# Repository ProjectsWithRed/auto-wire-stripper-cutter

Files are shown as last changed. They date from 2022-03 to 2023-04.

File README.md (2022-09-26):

# Automatic Wire Stripper and Cutter

A 3D printed automatic wire stripper and cutter. You simply choose your measurements on a screen, press a button, and it does it all for you. It will strip the wire and cut the wire depending on the options you chose.

There is a [video](https://youtu.be/pbuzLy1ktKM) associated with this repository/project, I highly recommend watching it before using this repo.

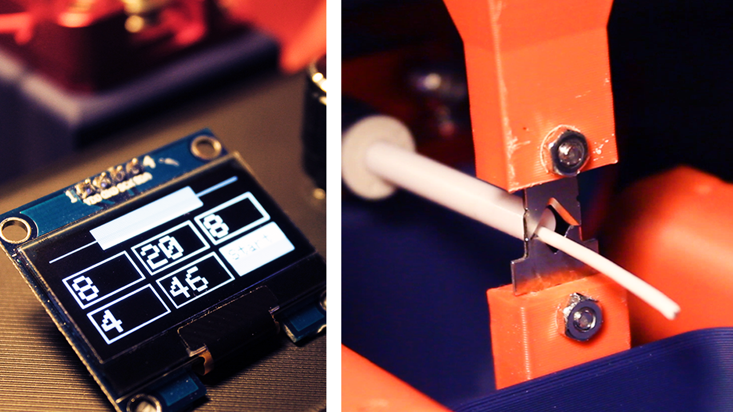
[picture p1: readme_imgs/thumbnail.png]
Video (https://youtu.be/pbuzLy1ktKM "Automatic_wire_stripper_cutter")


# Arduino

You can find the Arduino sketch in the `/AutoWireCutterStripper` directory.

- Make sure that the i2c address (`#define i2c_Address 0x3c`), corresponds to your OLED display i2c address, which you will find in the datasheet of your OLED display.

## Libraries needed

All these libraries can be easily installed using the Arduino IDE library manager.

- `Stepper` by Arduino.
- `Encoder` by Paul Stoffregen.
- `Adafruit GFX Library` by Adafruit.
- `Adafruit SH110X` by Adafruit.

# Components

- [ESP32](https://www.amazon.co.uk/dp/B071P98VTG?ref_=cm_sw_r_cp_ud_dp_DDGQ5R6XVBCC7JBB04K3), for the micro-controller. When uploading code, ensure that you hold down the on board BOOT button on the ESP32.
- [12V 5A](https://www.amazon.co.uk/dp/B08GS7WM1Z?ref_=cm_sw_r_cp_ud_dp_QJHEPBDAWDEDX3JDRTGF) power supply.
- [LM2596](https://www.amazon.co.uk/dp/B077VW4BTY?ref_=cm_sw_r_cp_ud_dp_1D9J5V36PP85VKDA2V49) or any step down converter, to convert 12V to 5V for the ESP32.
- [Nema 17 stepper motor](https://www.amazon.co.uk/dp/B07K3Y5314?ref_=cm_sw_r_cp_ud_dp_RZY0XHJFQ6YN1HZXPX8X) (x3), two for the linear motion, one for the extruder.
- [A4988 stepper motor driver](https://www.amazon.co.uk/dp/B06Y23YXD5?ref_=cm_sw_r_cp_ud_dp_1REVFHTFN5E2CMNSRTTB) (x3), to drive and control the stepper motors.
- 100uF capacitor (x3), for the 12V power pins for each of the A4988 drivers.
- [OLED display](https://www.amazon.co.uk/dp/B078J78R45?ref_=cm_sw_r_cp_ud_dp_1XXX2M7YAQJN5G6AKV93), 1.3inch, 128x64.
- [Rotary encoder](https://www.amazon.co.uk/dp/B07CMSHWV6?ref_=cm_sw_r_cp_ud_dp_Y2VC355RTHHYRKTZ436B) with button.
- [Power switch](https://www.amazon.co.uk/dp/B01N2U8PK0?ref_=cm_sw_r_cp_ud_dp_K4GSW1GDA4G8QCXJWPE4), to turn on and off.
- [3D printer filament extruder](https://www.amazon.co.uk/dp/B07TWK8FRN?ref_=cm_sw_r_cp_ud_dp_FXQD93NZKYG9VA0Q6P3F), for the wire feeder.
- [D8mm L100mm lead screw](https://www.amazon.co.uk/dp/B07QWKG317?ref_=cm_sw_r_cp_ud_dp_JMAC4EKE28W5Z3GSZSN8) (x2), for the linear motion.
- [D8mm lead screw nut](https://www.amazon.co.uk/dp/B07QWKG317?ref_=cm_sw_r_cp_ud_dp_JMAC4EKE28W5Z3GSZSN8) (x2), to attach the top blade housing to the lead screws.
- [5x8mm rigid shaft coupler](https://www.amazon.co.uk/dp/B096G1GZH5?ref_=cm_sw_r_cp_ud_dp_VWE1T2SQZQB0X13TQ1F7) (x2), to attach the lead screws to the stepper motors.
- [10mm magnets](https://www.amazon.co.uk/dp/B08FSTRRDR?ref_=cm_sw_r_cp_ud_dp_13WEC590XVADQKN2RJ0W) (x2), to attach the container.
- [KNIPEX V-blades](https://www.amazon.co.uk/dp/B00161GBDW?ref_=cm_sw_r_cp_ud_dp_S63KK1ZZ8DPRHWMBEFJC), to cut and strip the wires.

# Wiring

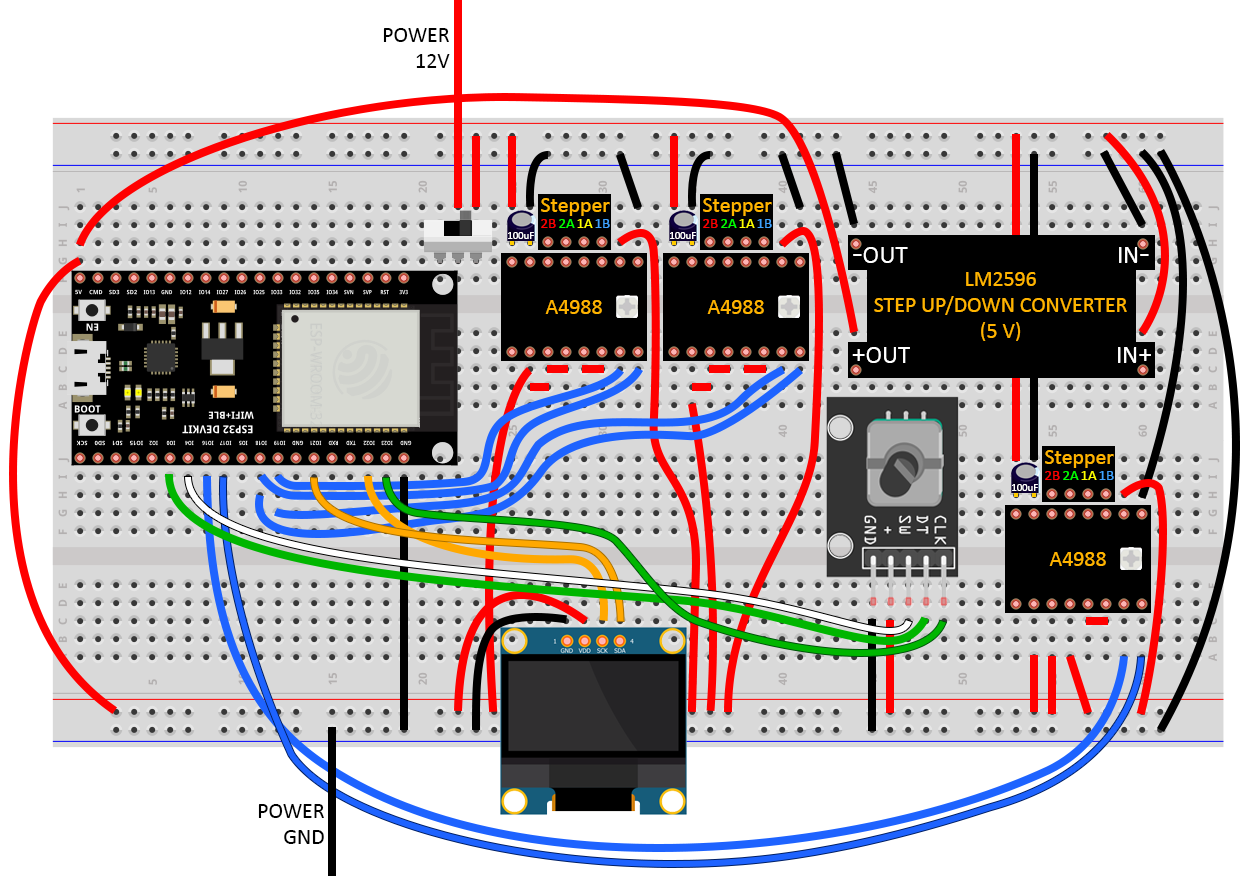
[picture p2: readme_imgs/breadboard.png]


# 3D printing

Please refer to the `/3d_printing` directory.

# Assembly layout
This is the layout of the components on the board. Use this only for reference on roughly where you should fix the components to the board. I don't suggest using this for exact measurements as you should position the components where it is appropriate for your version of the project.

[Layout PDF](./assembly_layout.pdf).

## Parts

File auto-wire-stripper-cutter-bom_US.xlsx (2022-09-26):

QTY | PN | Description | Cost/EA | Cost/EXT | Link | Notes
1 | ‎B08HMJ1X6W | ESP32-WROOM-32D | $19.59 | $19.59 | https://www.amazon.com/AITRIP-ESP32-DevKitC-Development-ESP32-WROOM-32D-Compatible/dp/B08HMJ1X6W | Micro Controller (Just get the three pack. You'll use em.)
1 | HTY-1205000 | DC 12V 5A Switching Power Supply | $13.88 | $13.88 | https://www.amazon.com/SUPERNIGHT-100V-Switching-Supply-Adapter/dp/B008FKDK2M | 12V 5A Power Supply
1 | B07L915WKX | LM2596 Adjustable Voltage Regulator | $9.09 | $9.09 | https://www.amazon.com/Aokin-Adjustable-Regulator-Converter-Voltmeter/dp/B07L915WKX | 12V to 5V Step Down for ESP32
1 | B088BLQYDX | Nema 17 Stepper Motor,42x23mm 42BYGH, 3 pack | $25.99 | $25.99 | https://www.amazon.com/Stepper-42x23mm-42BYGH-130mN-m-Printer/dp/B088BLQYDX | 2x Linear, 1x Extruder
1 | A4988 | HiLetgo 5pcs A4988 | $9.89 | $9.89 | https://www.amazon.com/HiLetgo-Stepstick-Stepper-Printer-Compatible/dp/B07BND65C8 | Stepper Motor Driver
1 | A-0002-F01f | Cap, Electrolytic, 100uF, 25V, 6 pack | $6.24 | $6.24 | https://www.amazon.com/Projects-Radial-Electrolytic-Capacitor-100uF/dp/B07YN6NX4H | For the 12V power pins for each of the A4988 drivers.
1 | 14284330 | OLED Display SSD1106 128x64 Pixels i2c | $12.49 | $12.49 | https://www.amazon.com/MakerFocus-128X64-1-3-Inch-SSD1106/dp/B08V97FYD2 | Display For machine
1 | KY-040 | Rotary Encoder Module KY-040, w Knob | $13.99 | $13.99 | https://www.amazon.com/TELESKY-Encoder-Potentiometers-%EF%BC%8815%C3%9716-5-Arduino/dp/B09T3CQ758 | Encoder to control
1 | U16F5 | Latching Illuminated 12V 5A Power Switch | $8.99 | $8.99 | https://www.amazon.com/Ulincos-Latching-Button-Suitable-Mounting/dp/B07FVHRM1F | Power Switch
1 | RDX3D030B-PASFQ | Redrex Ender 3 Extruder | $10.99 | $10.99 | https://www.amazon.com/dp/B08CS9THQL?th=1 | Wire Extruder
1 | a19032000ux0497 | 2X 100mm Lead Screw w/ Nut | $11.99 | $11.99 | https://www.amazon.com/uxcell-Stainless-Copper-Thread-Printer/dp/B07QX4KP8Y | Linear Motion for Guillotine (Lead Screw and Nut Combo)
1 | 0791783537158 | 2X 5mm to 8mm rigid coupler | $8.54 | $8.54 | https://www.amazon.com/Zeberoxyz-Coupling-Aluminum-Diameter-Connector/dp/B08ZJ854Z6 | Linear NEMA 17 Coupler
1 | B09XMHCLYG | 30X 10x2mm magnets | $7.99 | $7.99 | https://www.amazon.com/Fridge-Magnets-Refrigerator-Neodymium-Whiteboard/dp/B09XMHCLYG | For attaching container
1 | 12 69 21 | Blades for Knipex 12 62 180 | $17.87 | $17.87 | https://www.amazon.com/KNIPEX-12-69-21-Blades/dp/B005GYL20M | For Cutting Wires…and things…
 |  |  |  | $177.53
1 | B094HYN8T2 | 4x4 Matrix Keypad, 6 pack | $8.99 | $8.99 | https://www.amazon.com/Keypad-Membrane-Keyboard-Arduino-Microcontroller/dp/B094HYN8T2 | For direct data input
https://github.com/ProjectsWithRed/auto-wire-stripper-cutter

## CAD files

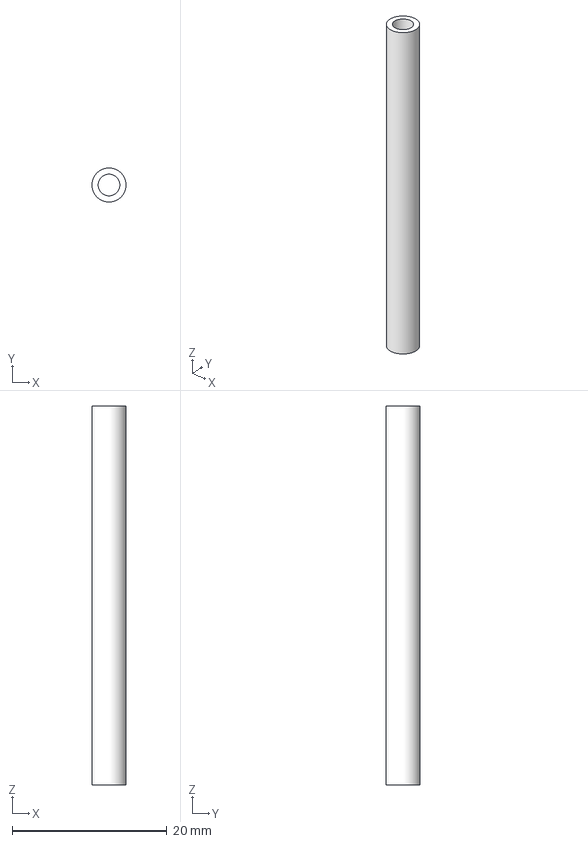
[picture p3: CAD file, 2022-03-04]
3d_printing/wire_channel.3mf
4.40 x 4.40 x 49.0 mm

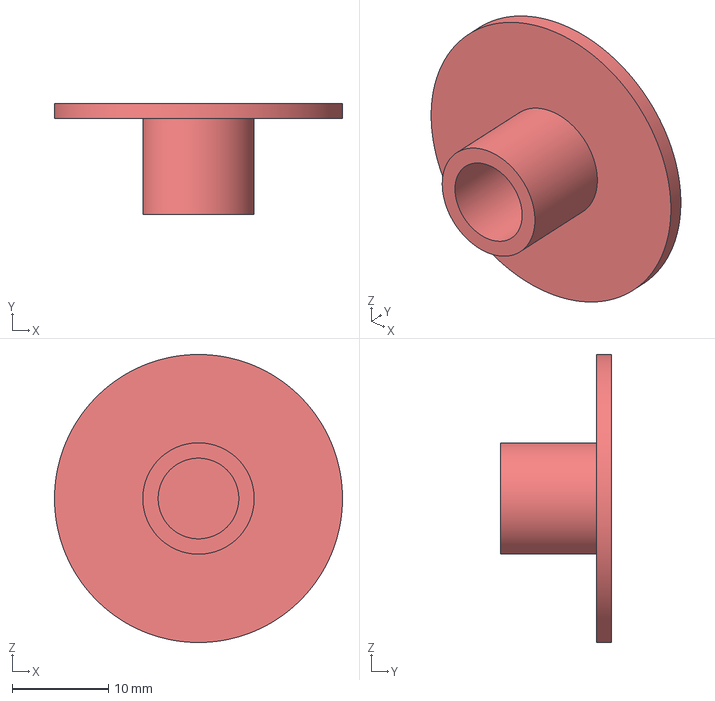
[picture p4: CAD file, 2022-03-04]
3d_printing/spoolHolder_cylinder_cap.3mf
30.0 x 11.6 x 30.0 mm

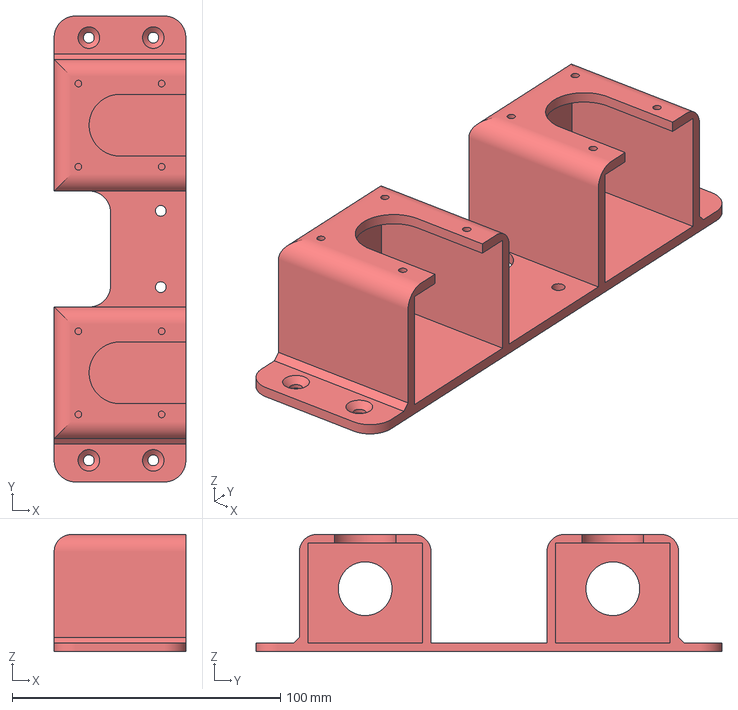
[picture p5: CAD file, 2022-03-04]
3d_printing/linearMotion_motorsHousing.3mf
49.0 x 173.6 x 43.6 mm

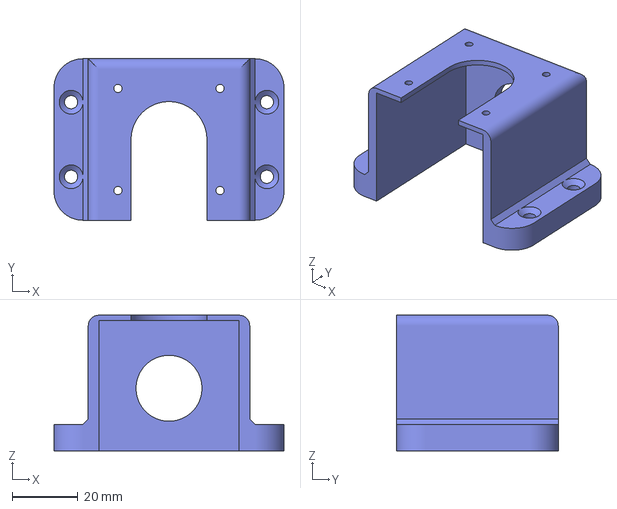
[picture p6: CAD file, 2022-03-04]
3d_printing/extruderStepper_housing.3mf
69.8 x 49.0 x 41.2 mm

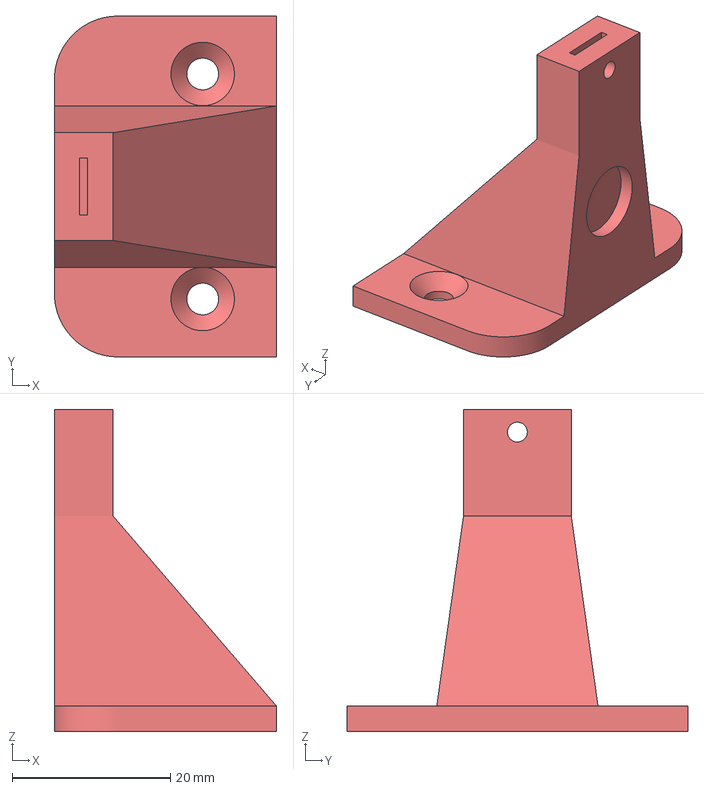
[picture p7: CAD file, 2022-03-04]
3d_printing/bottomBlade_housing.3mf
28.0 x 43.0 x 40.6 mm

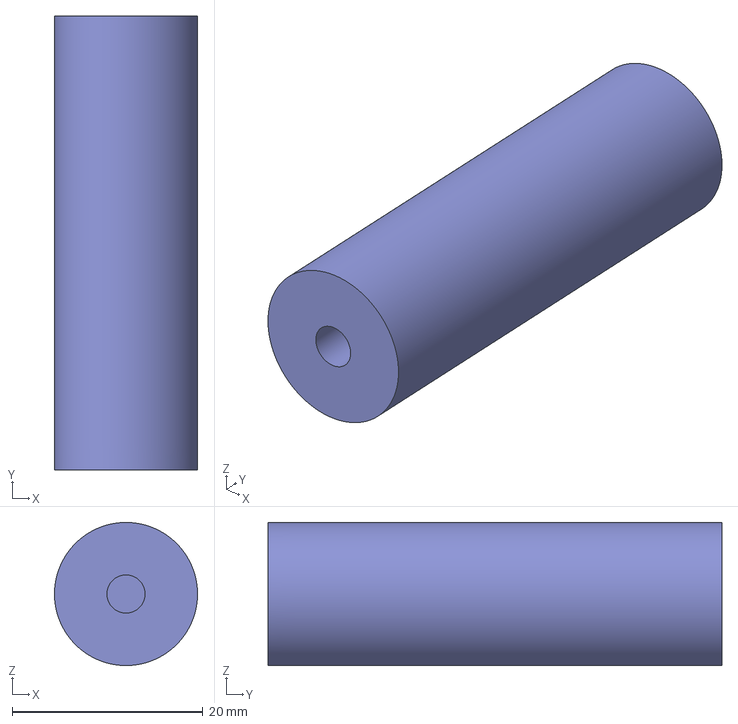
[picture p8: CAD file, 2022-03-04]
3d_printing/spoolHolder_cylinder.3mf
15.0 x 47.6 x 15.0 mm

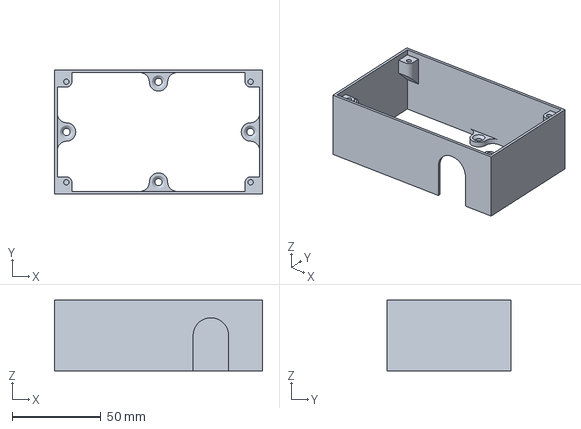
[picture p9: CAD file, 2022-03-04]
3d_printing/wiring_housing.3mf
117.4 x 70.2 x 40.0 mm

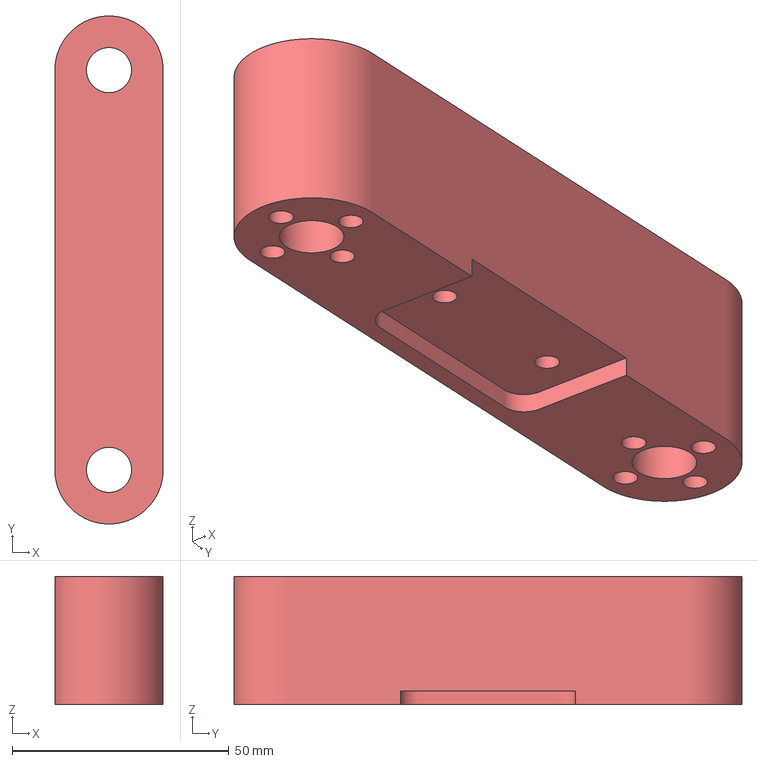
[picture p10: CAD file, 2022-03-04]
3d_printing/linearMotion_attachment.3mf
25.0 x 117.2 x 29.6 mm

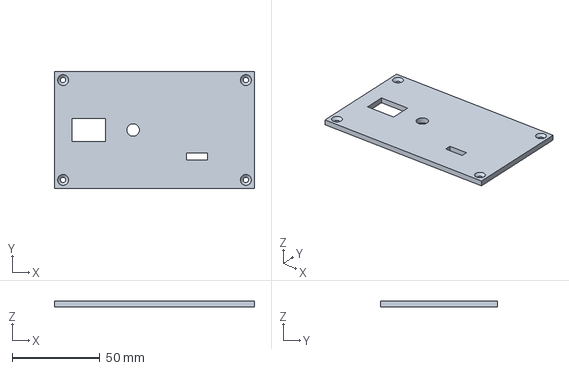
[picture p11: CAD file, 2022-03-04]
3d_printing/wiring_housing_lid.3mf
113.8 x 66.6 x 3.20 mm

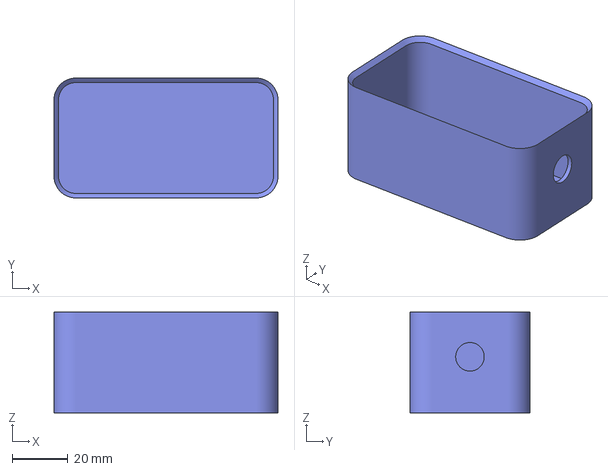
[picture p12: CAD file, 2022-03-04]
3d_printing/container.3mf
80.0 x 42.8 x 36.0 mm

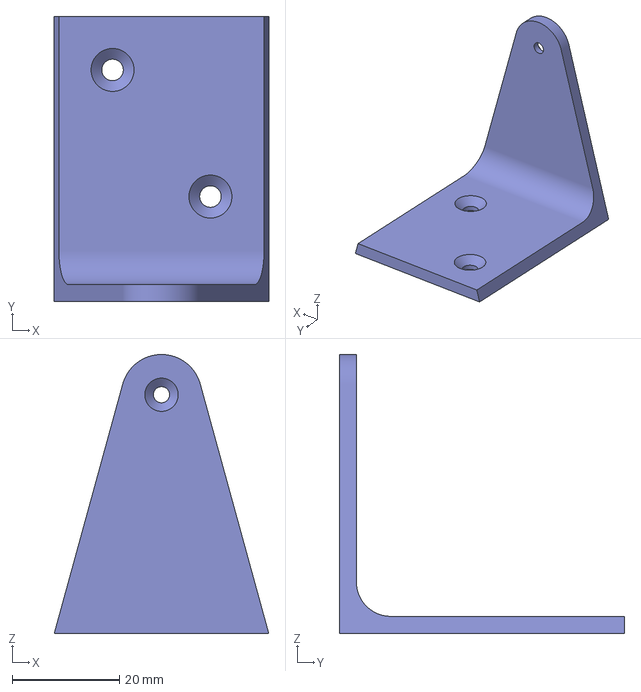
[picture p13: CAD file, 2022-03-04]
3d_printing/spoolHolder_base.3mf
40.0 x 53.2 x 52.0 mm

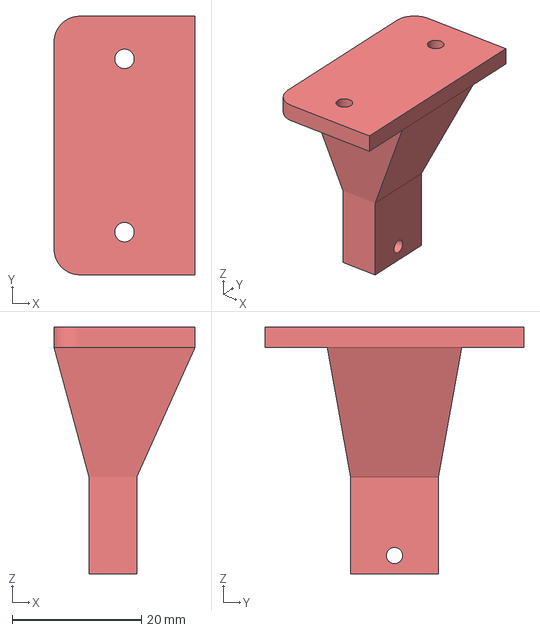
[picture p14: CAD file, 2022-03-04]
3d_printing/topBlade_housing.3mf
21.8 x 40.0 x 38.2 mm

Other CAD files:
3d_printing/stl/bottomBlade_housing.stl
3d_printing/stl/container.stl
3d_printing/stl/extruderStepper_housing.stl
3d_printing/stl/spoolHolder_base.stl
3d_printing/stl/spoolHolder_cylinder.stl
3d_printing/stl/spoolHolder_cylinder_cap.stl
3d_printing/stl/topBlade_housing.stl
3d_printing/stl/wiring_housing.stl
3d_printing/stl/wiring_housing_lid.stl

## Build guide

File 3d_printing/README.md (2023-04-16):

# 3D printing

All the 3D printed parts used in this project.

- `/stl`, same models but in stl format.
- `assembly_model.step`, the full design in `.step` format.

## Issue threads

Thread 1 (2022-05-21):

PCB layout and assembly installation layout

umalave, 2022-05-21:
Hi, do you have a PCB layout for this project? also, do you have the layout where you attached the threaded insert on the wood board?

ProjectsWithRed, 2022-05-23:
Hi,

I did not create a PCB layout for this project.

Regarding the assembly layout, I just added a PDF (ee4eb457c4b8973d444eb9b3b2031fe7ea3d9ca9) showing the assembly layout. However, I recommend using it only for reference on roughly where you should fix the components to the board. I don't suggest using this for exact measurements as you should position the components where it is appropriate for your version of the project.

Closed 2022-07-25.

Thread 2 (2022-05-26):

Printable baseplate with heat set inserts

fryertruck, 2022-05-26:
I really appreciate your work in this project and thinking about building one.

What do you think about adding a printable base to your project? Of course the positions would then be fixed, but I don't see an Issue with that.

I can help you out with creating the file, but need correct measurements for that.

ProjectsWithRed, 2022-06-22:
I have uploaded a file `assembly_layout.pdf` that shows all the measurements on the board, feel free do make a printable base 👍🏼.

Closed 2022-07-25.

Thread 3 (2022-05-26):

Let the machine remove part of the Insulation

fryertruck, 2022-05-26:
Is it possible that the machine also directly removes the insulation from the front part of the cable? Before the blade goes up again, the extruder would have to pull back for this in the first step.

Can you perhaps test this?

ProjectsWithRed, 2022-06-22:
You can easily achieve this with minimal changes to the code and if done correctly should work with no issues. Feel free to experiement, as I unfortunately don't have time to do it.

ProjectsWithRed, 2022-07-25:
Inactive.

Closed 2022-07-25.

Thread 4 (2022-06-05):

Having issues loading the code. Can you help, please?

umalave, 2022-06-05:
Arduino: 1.8.19 (Windows 10), Board: "DOIT ESP32 DEVKIT V1, 80MHz, 115200, None"

AutoWireCutterStripper:60:71: error: stray '\302' in program

   <title>auto-wire-stripper-cutter/AutoWireCutterStripper.ino at main · ProjectsWithRed/auto-wire-stripper-cutter · GitHub</title>

                                                                       ^

AutoWireCutterStripper:60:72: error: stray '\267' in program

   <title>auto-wire-stripper-cutter/AutoWireCutterStripper.ino at main · ProjectsWithRed/auto-wire-stripper-cutter · GitHub</title>

                                                                        ^

AutoWireCutterStripper:60:116: error: stray '\302' in program

   <title>auto-wire-stripper-cutter/AutoWireCutterStripper.ino at main · ProjectsWithRed/auto-wire-stripper-cutter · GitHub</title>

                                                                                                                    ^

AutoWireCutterStripper:60:117: error: stray '\267' in program

   <title>auto-wire-stripper-cutter/AutoWireCutterStripper.ino at main · ProjectsWithRed/auto-wire-stripper-cutter · GitHub</title>

                                                                                                                     ^

C:\Users\myuser\Desktop\AutoWireCutterStripper\AutoWireCutterStripper.ino:411:10: warning: missing terminating ' character

     <!-- '"` --><!-- </textarea></xmp> --></option></form><form class="js-site-search-form" role="search" aria-label="Site" data-scope-type="Repository" data-scope-id="466200308" data-scoped-search-url="/ProjectsWithRed/auto-wire-stripper-cutter/search" data-owner-scoped-search-url="/users/ProjectsWithRed/search" data-unscoped-search-url="/search" data-turbo="false" action="/ProjectsWithRed/auto-wire-stripper-cutter/search" accept-charset="UTF-8" method="get">

          ^

AutoWireCutterStripper:411:10: error: missing terminating ' character

     <!-- '"` --><!-- </textarea></xmp> --></option></form><form class="js-site-search-form" role="search" aria-label="Site" data-scope-type="Repository" data-scope-id="466200308" data-scoped-search-url="/ProjectsWithRed/auto-wire-stripper-cutter/search" data-owner-scoped-search-url="/users/ProjectsWithRed/search" data-unscoped-search-url="/search" data-turbo="false" action="/ProjectsWithRed/auto-wire-stripper-cutter/search" accept-charset="UTF-8" method="get">

          ^~~~~~~~~~~~~~~~~~~~~~~~~~~~~~~~~~~~~~~~~~~~~~~~~~~~~~~~~~~~~~~~~~~~~~~~~~~~~~~~~~~~~~~~~~~~~~~~~~~~~~~~~~~~~~~~~~~~~~~~~~~~~~~~~~~~~~~~~~~~~~~~~~~~~~~~~~~~~~~~~~~~~~~~~~~~~~~~~~~~~~~~~~~~~~~~~~~~~~~~~~~~~~~~~~~~~~~~~~~~~~~~~~~~~~~~~~~~~~~~~~~~~~~~~~~~~~~~~~~~~~~~~~~~~~~~~~~~~~~~~~~~~~~~~~~~~~~~~~~~~~~~~~~~~~~~~~~~~~~~~~~~~~~~~~~~~~~~~~~~~~~~~~~~~~~~~~~~~~~~~~~~~~~~~~~~~~~~~~~~~~~~~~~~~~~~~~~~~~~~~~~~~~~~~~~~~~~~~~~~~~~~~~~~~~~~~~~~~~~~~~~~~~~~~~~~~~~

AutoWireCutterStripper:468:75: error: stray '\342' in program

       <span aria-hidden="true" class="d-inline-block ml-1 v-align-middle">↵</span>

                                                                           ^

AutoWireCutterStripper:468:76: error: stray '\206' in program

       <span aria-hidden="true" class="d-inline-block ml-1 v-align-middle">↵</span>

                                                                            ^

AutoWireCutterStripper:468:77: error: stray '\265' in program

       <span aria-hidden="true" class="d-inline-block ml-1 v-align-middle">↵</span>

                                                                             ^

AutoWireCutterStripper:473:56: error: stray '\342' in program

       <span class="d-inline-block ml-1 v-align-middle">↵</span>

                                                        ^

AutoWireCutterStripper:473:57: error: stray '\206' in program

       <span class="d-inline-block ml-1 v-align-middle">↵</span>

                                                         ^

AutoWireCutterStripper:473:58: error: stray '\265' in program

       <span class="d-inline-block ml-1 v-align-middle">↵</span>

                                                          ^

AutoWireCutterStripper:515:75: error: stray '\342' in program

       <span aria-hidden="true" class="d-inline-block ml-1 v-align-middle">↵</span>

                                                                           ^

AutoWireCutterStripper:515:76: error: stray '\206' in program

       <span aria-hidden="true" class="d-inline-block ml-1 v-align-middle">↵</span>

                                                                            ^

AutoWireCutterStripper:515:77: error: stray '\265' in program

       <span aria-hidden="true" class="d-inline-block ml-1 v-align-middle">↵</span>

                                                                             ^

AutoWireCutterStripper:520:56: error: stray '\342' in program

       <span class="d-inline-block ml-1 v-align-middle">↵</span>

                                                        ^

AutoWireCutterStripper:520:57: error: stray '\206' in program

       <span class="d-inline-block ml-1 v-align-middle">↵</span>

                                                         ^

AutoWireCutterStripper:520:58: error: stray '\265' in program

       <span class="d-inline-block ml-1 v-align-middle">↵</span>

                                                          ^

AutoWireCutterStripper:553:75: error: stray '\342' in program

       <span aria-hidden="true" class="d-inline-block ml-1 v-align-middle">↵</span>

                                                                           ^

AutoWireCutterStripper:553:76: error: stray '\206' in program

       <span aria-hidden="true" class="d-inline-block ml-1 v-align-middle">↵</span>

                                                                            ^

AutoWireCutterStripper:553:77: error: stray '\265' in program

       <span aria-hidden="true" class="d-inline-block ml-1 v-align-middle">↵</span>

                                                                             ^

AutoWireCutterStripper:558:56: error: stray '\342' in program

       <span class="d-inline-block ml-1 v-align-middle">↵</span>

                                                        ^

AutoWireCutterStripper:558:57: error: stray '\206' in program

       <span class="d-inline-block ml-1 v-align-middle">↵</span>

                                                         ^

AutoWireCutterStripper:558:58: error: stray '\265' in program

       <span class="d-inline-block ml-1 v-align-middle">↵</span>

                                                          ^

AutoWireCutterStripper:591:75: error: stray '\342' in program

       <span aria-hidden="true" class="d-inline-block ml-1 v-align-middle">↵</span>

                                                                           ^

AutoWireCutterStripper:591:76: error: stray '\206' in program

       <span aria-hidden="true" class="d-inline-block ml-1 v-align-middle">↵</span>

                                                                            ^

AutoWireCutterStripper:591:77: error: stray '\265' in program

       <span aria-hidden="true" class="d-inline-block ml-1 v-align-middle">↵</span>

                                                                             ^

AutoWireCutterStripper:596:56: error: stray '\342' in program

       <span class="d-inline-block ml-1 v-align-middle">↵</span>

                                                        ^

AutoWireCutterStripper:596:57: error: stray '\206' in program

       <span class="d-inline-block ml-1 v-align-middle">↵</span>

                                                         ^

AutoWireCutterStripper:596:58: error: stray '\265' in program

       <span class="d-inline-block ml-1 v-align-middle">↵</span>

                                                          ^

C:\Users\umala\Desktop\AutoWireCutterStripper\AutoWireCutterStripper.ino:977:25: warning: missing terminating " character

             data-action="

                         ^

AutoWireCutterStripper:977:25: error: missing terminating " character

AutoWireCutterStripper:978:41: error: stray '#' in program

               input-entered:ref-selector#inputEntered

                                         ^

AutoWireCutterStripper:979:40: error: stray '#' in program

               tab-selected:ref-selector#tabSelected

                                        ^

AutoWireCutterStripper:980:38: error: stray '#' in program

               focus-list:ref-selector#focusFirstListMember

                                      ^

C:\Users\umala\Desktop\AutoWireCutterStripper\AutoWireCutterStripper.ino:981:13: warning: missing terminating " character

             "

             ^

AutoWireCutterStripper:981:13: error: missing terminating " character

C:\Users\umala\Desktop\AutoWireCutterStripper\AutoWireCutterStripper.ino:1028:25: warning: missing terminating " character

             data-action="

                         ^

AutoWireCutterStripper:1028:25: error: missing terminating " character

AutoWireCutterStripper:1029:41: error: stray '#' in program

               input-entered:ref-selector#inputEntered

                                         ^

AutoWireCutterStripper:1030:40: error: stray '#' in program

               tab-selected:ref-selector#tabSelected

                                        ^

AutoWireCutterStripper:1031:38: error: stray '#' in program

               focus-list:ref-selector#focusFirstListMember

                                      ^

C:\Users\umala\Desktop\AutoWireCutterStripper\AutoWireCutterStripper.ino:1032:13: warning: missing terminating " character

             "

             ^

AutoWireCutterStripper:1032:13: error: missing terminating " character

AutoWireCutterStripper:1398:71: error: stray '#' in program

           <td id="LC1" class="blob-code blob-code-inner js-file-line">#<span class="pl-k">include</span> <span class="pl-s"><span class="pl-pds">&lt;</span>Stepper.h<span class="pl-pds">&gt;</span></span></td>

                                                                       ^

AutoWireCutterStripper:1402:71: error: stray '#' in program

           <td id="LC2" class="blob-code blob-code-inner js-file-line">#<span class="pl-k">include</span> <span class="pl-s"><span class="pl-pds">&lt;</span>Encoder.h<span class="pl-pds">&gt;</span></span></td>

                                                                       ^

AutoWireCutterStripper:1406:71: error: stray '#' in program

           <td id="LC3" class="blob-code blob-code-inner js-file-line">#<span class="pl-k">include</span> <span class="pl-s"><span class="pl-pds">&lt;</span>SPI.h<span class="pl-pds">&gt;</span></span></td>

                                                                       ^

AutoWireCutterStripper:1410:71: error: stray '#' in program

           <td id="LC4" class="blob-code blob-code-inner js-file-line">#<span class="pl-k">include</span> <span class="pl-s"><span class="pl-pds">&lt;</span>Wire.h<span class="pl-pds">&gt;</span></span></td>

                                                                       ^

AutoWireCutterStripper:1414:71: error: stray '#' in program

           <td id="LC5" class="blob-code blob-code-inner js-file-line">#<span class="pl-k">include</span> <span class="pl-s"><span class="pl-pds">&lt;</span>Adafruit_GFX.h<span class="pl-pds">&gt;</span></span></td>

                                                                       ^

AutoWireCutterStripper:1418:71: error: stray '#' in program

           <td id="LC6" class="blob-code blob-code-inner js-file-line">#<span class="pl-k">include</span> <span class="pl-s"><span class="pl-pds">&lt;</span>Adafruit_SH110X.h<span class="pl-pds">&gt;</span></span></td>

                                                                       ^

AutoWireCutterStripper:1427:71: error: stray '#' in program
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

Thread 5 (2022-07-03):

Arduino Programming issue

JoeKingSid, 2022-07-03:
Hello, I cannot seem to connect to my ESP board to upload the Sketch.  I think it is because I do not have the correct board selected.  I purchased this board [https://www.amazon.com/dp/B09J95SMG7?ref=ppx_yo2ov_dt_b_product_details&th=1](url) installed the required libraries but upon upload get an error message that states my board is not connected.  FYI... I have connected power, the screen and the pot on a breadboard just to keep things simple to start.  Can you advise what I need to do to get my Board to talk to my Computer?  Thanks!

JoeKingSid, 2022-07-04:
Here is a screen shot of the error message as well as my Board Config

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
g

JoeKingSid, 2022-07-04:
1 More shot of Device Manager recognizing the port 5 connection.  Thanks in advance for any advice/help!
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

ProjectsWithRed, 2022-07-04:
Try selecting "ESP32 Dev Module" as the board. Also press and hold the boot button on the ESP32 when you press upload.

JoeKingSid, 2022-07-04:
Well, actually I might have spoken a bit too soon ...  I found this thing in Arduino called Serial Monitor...  it seems to show that the Controller has some kind of error and is stuck in some kind of a Reboot Loop...  this is what it says...

ELF file SHA256: 0000000000000000

Rebooting...
ets Jul 29 2019 12:21:46

rst:0xc (SW_CPU_RESET),boot:0x13 (SPI_FAST_FLASH_BOOT)
configsip: 0, SPIWP:0xee
clk_drv:0x00,q_drv:0x00,d_drv:0x00,cs0_drv:0x00,hd_drv:0x00,wp_drv:0x00
mode:DIO, clock div:1
load:0x3fff0030,len:1344
load:0x40078000,len:13516
load:0x40080400,len:3604
entry 0x400805f0
E (121) gpio: esp_ipc_call_blocking failed (0x103)
E (121) gpio: gpio_install_isr_service(449): GPIO isr service already installed
Guru Meditation Error: Core  0 panic'ed (LoadProhibited). Exception was unhandled.

Core  0 register dump:
PC      : 0x400ee48b  PS      : 0x00060533  A0      : 0x800d4d4f  A1      : 0x3ffe3b20
A2      : 0x00000000  A3      : 0x3ffc1c38  A4      : 0x3ffc1c38  A5      : 0x00060523
A6      : 0x00060520  A7      : 0x00000001  A8      : 0x800d490c  A9      : 0x3ffe3ae0
A10     : 0x3ffbdca4  A11     : 0x00800000  A12     : 0x00000017  A13     : 0x3ffe3b20
A14     : 0x007bdc90  A15     : 0x003fffff  SAR     : 0x00000009  EXCCAUSE: 0x0000001c
EXCVADDR: 0x00000000  LBEG    : 0x400865e5  LEND    : 0x400865f5  LCOUNT  : 0xfffffff7

Backtrace:0x400ee488:0x3ffe3b200x400d4d4c:0x3ffe3b40 0x400d2cf4:0x3ffe3b70 0x400d2d75:0x3ffe3ba0 0x400d13b9:0x3ffe3bc0 0x400d15b9:0x3ffe3be0 0x400d96ab:0x3ffe3c10 0x40082ce1:0x3ffe3c40 0x4007920a:0x3ffe3c90  |<-CORRUPTED

ELF file SHA256: 0000000000000000

Rebooting...
ets Jul 29 2019 12:21:46

rst:0xc (SW_CPU_RESET),boot:0x13 (SPI_FAST_FLASH_BOOT)

It just keeps repeating that over and over.  Any ideas???  I wish you would make a video showing details of how to upload the INO cause so far everything else has been straightforward but, to a NOOB like me, the Arduino programming is not very intuitive.  THANKS!!!

ProjectsWithRed, 2022-07-08:
@JoeKingSid Someone had this similar problem, please see issue #4. To fix it, try uploading the code using the Arduino web IDE.

JoeKingSid, 2022-07-23:
UPDATE... First let me say thanks for the suggestions thus far!  To date I have still not been able to get the project working. :-( I was able to upload code via the Online Web Editor and I think that part is complete but honestly I'm not sure. After uploading the code I was expecting to see my OLED display light up with something but, No Joy.  I decided to start from scratch and these are the steps I took...
1. Connect the ESP32 to the Computer via USB cable.
2. Upload Code
3. Place ESP32 chip on Breadboard and connect  12vdc adapter to Stepdown Converter
4. verify 5vdc on stepdown and connect  5vdc wires as shown on diagram to ESP32 & OLED display
5. Connect OLED SDK & SDA  to ESP Pins 21 & 22 as shown
6. Connect Pot/Encoder to 5VDC (as shown) & SW, DT & SDK to ESP32 Pins  as shown.

applied power to circuit - nothing
pressed enable button on ESP32 - nothing
pressed boot button on ESP32 -nothing

Tried Re-uploading the code - nothing

Not really sure what else to try as this seems to be the "bare bones" setup in which something should come to life.

I've done lots of programming on Industrial PLC's and also have worked with the Arduino MEGA 2560 series of boards/ uploaded code successfully and don't understand what I am doing wrong that is causing me so many issues.

I really do like the idea of this project and would like to realize success but I'm thinking that perhaps the ESP32 controller is not the best way to go for me?  Was going to look at maybe trying to convert this over to some other Native Arduino Board format and giving it a go that way?

Any advice is certainly appreciated!  Thanks in advance and I hope somebody somewhere has an idea of how to get things going!

ProjectsWithRed, 2022-07-25:
Hello Joe, thank you for all this information. I would suggest completing all of the wiring on the breadboard, then turning everything on. I have not tested the code with partial wiring of the components. I think that is what is causing you issues. So complete the full wiring, send me a picture of it if you can and we will go from there.

ProjectsWithRed, 2022-07-25:
@JoeKingSid Also, just to make sure, did you change the i2c address of your OLED display in the code? Make sure `#define i2c_Address 0x3c` corresponds to the address of your OLED display which you will find out from the datasheet of the OLED display. If you did not change this, try again without the full wiring.

JoeKingSid, 2022-07-25:
OK, Thanks I will try those items and report back!

JoeKingSid, 2022-07-31:
OK!  Success!!!

BTW - It is possible to test the display without all the wiring being connected.  I was able to achieve this by using the 3.3v output from the ESP32 (instead of the 12vdc/5vdc system that is shown on your schematic. After verifying that the display/pot were working in this config, I switched back to the shown design and found loose connections in the 5VDC distribution and analog outputs which were causing my problems.

Also, I was only able to upload the INO if I hold down the ENABLE Button on the ESP32 while it is compiling/Uploading which I feel should definitely be mentioned.

Thanks much for your help/patience! Now, let's get those wires STRIPPED!!!

ProjectsWithRed, 2022-08-01:
This is great to hear! I am glad everything worked out 👍🏼.

Closed 2022-08-01.

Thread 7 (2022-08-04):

Fusion Repo?

jrsteensen, 2022-08-04:
Hello! I was just curious if the Fusion repository was  publicly available? I'm going to build this but wanted to make a few changes in MCAD for personal preferences. Fantastic project and really excited to work on it.

Thanks!

ProjectsWithRed, 2022-08-24:
Unfortunately I can't provide the Fusion 360 file, however, feel free to import the model to F360 and modify it with the editing tools to meet your needs 👍🏼.

leahcornelius, 2023-04-14:
Hi, I was wondering if it is specifically F360 files you can't provide or general-cad files. Would you be able to export a .step file or similar, or is it that you cannot upload the CAD designs themselves (completely understandable, I've had projects myself I wasn't allowed to publish the cad for).

Really awesome work though! Just a few changes and tweaks I want to add - I can try and remake the CAD bodies using the 3mf files but if you have them to hand already would be silly to do so.

ProjectsWithRed, 2023-04-16:
@leahcornelius The stl files are also available in the [stl directory](https://github.com/ProjectsWithRed/auto-wire-stripper-cutter/tree/main/3d_printing/stl), are you not able to use those?

ProjectsWithRed, 2023-04-16:
@leahcornelius The stl files are also available in the [stl directory](https://github.com/ProjectsWithRed/auto-wire-stripper-cutter/tree/main/3d_printing/stl), are you able to use those?

leahcornelius, 2023-04-16:
Sadly not, as they are meshes and so cannot be edited in cad software simply. I could convert them into bodys/cad files manually but will probably just produce my own designs for now as it will take the same amount of time. Awesome work though! Its a really well thoight out design and will be a solid inspiration for projects

ProjectsWithRed, 2023-04-16:
@leahcornelius Will `.step` files help you? Let me know what extension is best for you. Thanks! I appreciate that.

leahcornelius, 2023-04-16:
@ProjectsWithRed yeah step files would be great! I use fusion 360 so .f3d, .step, all work. Thanks

ProjectsWithRed, 2023-04-16:
@leahcornelius You can now find the `.step` file for the full design in `3d_printing/assembly_model.step` 👍🏼.

leahcornelius, 2023-04-16:
Thanks, i appricate it!

Closed 2022-09-02.

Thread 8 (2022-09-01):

Serial monitor problems

dhardyuk, 2022-09-01:
I usually stick some variables in the start of the code with the sketch name and version etc. This then gets output to the serial monitor and/or displayed on the screen as part of the setup() code.

So I've copied over your code and added this to the variables section at the top after the #includes:

//Name and version
const String progname = "Wire Cut and Strip";
const String progver = "0.01";

And this to the start of the setup() code:

// push out some details over the serial port
//    delay(2000);
//    Serial.begin(9600);//Set up serial stream
//    delay(2000);
//    Serial.print("Programe Name: ");
//    Serial.print (progname);
//    Serial.print ("\n");
//    Serial.print("Version:       ");
//    Serial.print (progver);
//    Serial.print ("\n");
//    delay(2000);
//    Serial.end();//end serial stream

So far so good. However, when I remove the // for the Serial output stuff the serial monitor just loops through this text:

20:11:33.156 -> Programe Name: Wire Cut and Strip
20:11:33.200 -> Version:       0.01
20:11:39.169 -> Programe Name: Wire Cut and Strip
20:11:39.169 -> Version:       0.01
20:11:45.178 -> Programe Name: Wire Cut and Strip
20:11:45.178 -> Version:       0.01
20:11:51.156 -> Programe Name: Wire Cut and Strip
20:11:51.202 -> Version:       0.01
20:11:57.160 -> Programe Name: Wire Cut and Strip
20:11:57.205 -> Version:       0.01

This is lifted straight from my other sketches, with the variables set to different values. Any idea why this is happening or where I should start trying to debug?

I don't have anything else connected, no buttons or rotary encoder

I have adjusted your code slightly to make if fit an Arduino Nano v3.0 on a 3 Stepper CNC shield HW-702 - the tweaks needed are to set the pins for the A4988 stepper drivers to suit the board (so using Y axis stepper pins 6 and 3 for extruder and Z axis stepper pins 7 and 4) The temporary setup buttons are on 5 and 8, the encoder DT and clock are 12 and 13, and the encoder button is 9. However, ignoring all that and using your code without those tweaks gets me to the correct display.

dhardyuk, 2022-09-01:
Update - rotary encoders delivered so I have that part installed and working.

dhardyuk, 2022-09-02:
To add to the above, the looping happens and the screen never gets drawn. Its power cycling after the setup() code. Comment out the serial code and it runs find.

ProjectsWithRed, 2022-09-02:
Hello! It looks like it's rebooting everytime which is causing the "loop" of the setup function. Below are some things that may help you debug the problem.

- You might have connected something to the reset pins of the micro-controller, or to pins that should not be used, so do double check the datasheet to ensure you are not using pins that you shouldn't be using.
- Try keeping all Serial statements uncommented apart from `Serial.end()`.
- Start a new blank sketch, with nothing connected to the micro-controller, add your code, run it to ensure all good, then slowly, bit by bit add components and code to see exactly what is causing the problem.

Let me know how it goes👍.

dhardyuk, 2022-09-02:
It fails the same way. It has to be something weird!

ProjectsWithRed, 2022-09-02:
Yes it is! Did you manage to do point 3 that I mentioned? At what point did it fail?

One quick thing to try is, remove the string variables that you have, `progname` and `progver`, and where you have referenced them just use a hard-coded string value.

Side note: Rather than doing `Serial.print ("\n");`, just use `Serial.println()` in the previous statement, it will add a line break at the end for you.

ProjectsWithRed, 2022-09-28:
@dhardyuk Was this issue fixed?

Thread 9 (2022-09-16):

Motor only turns once and stops

GuilhermeLeonidio, 2022-09-16:
hello, how are you? I'm using the green A9488 module instead of the red one and I'm trying to make only one engine work but it spins for about 5 seconds and doesn't do anything else, I didn't add any more lines in the code and I didn't put any numbers or letters plus this is 100% original. I would like to know if there is something that needs to be put in the code or needs the three engines to work, I would be grateful if you answer me this would help me a lot my friend
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

ProjectsWithRed, 2022-09-16:
Yes you are supposed to make some changes to the code, and the changes are commented directly in the code, so I recommend going through the code and reading the comments to see exactly what changes you need to make and how to use it.

By default, calibration mode will be on (see the `CALIBRATION_MODE` variable).

Are you referring to the stepper motor as the "engine"? If so, does it turn when you turn on power, or after you press the rotatary encoder?

GuilhermeLeonidio, 2022-09-16:
Hello all well? it spins after pressing the rotary encoder, I'm going through and reading the comments but I'm quite a layman in this part of c++ communication could you give me some help in this part of the adjustment? a picture of something like that with the modifications

GuilhermeLeonidio, 2022-09-16:
I need to set the calibration_MODR to false ?

AV1987, 2022-09-24:
How did you get the Oled display turned on? Mine doesn't display.

ProjectsWithRed, 2022-09-28:
@GuilhermeLeonidio `CALIBRATION_MODE` is used to adjust `WIRE_MOVEMENT_MULTI` to make sure the extruder stepper motor (the one that moves the wire) gives the correct wire length. So if you have `CALIBRATION_MODE` to true, you need to put a number on the first cell (top left, only that cell will work in calibration mode). So now when you press the encoder, the wire will feed and then the blades will cut the wire without stripping, then you need to measure the wire length, and see if it is longer or shorter than the measurement you put in the first cell, and from there adjust `WIRE_MOVEMENT_MULTI` to be higher or lower depending if the wire was longer or shorter than the measurement you put in the first cell.

After you have achieved the correct wire sizes, you can then make `CALIBRATION_MODE` to false, since you have now finished the calibration.

If you want to run the machine without calibration, just make `CALIBRATION_MODE` to false, however, the wire lengths might not be accurate, since why you need to calibrate.

Let me know if you have any questions.

Closed 2023-04-16.

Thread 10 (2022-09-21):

First wiring: the 3 stepper motor turn slowly

Parang0n, 2022-09-21:
hello and firstly , thanks for you DIY! this is a masterpiece that i NEED to see working ( on my house °_° ) , sorry for my english ( hello from france )

i have make all the wirring and when i start the wire cutter , ( 1st the screen is black ) , but most important the 3 motor turn very slowly and seems to dont want stop

lm2596 IN : 12V  OUT: 5.08V

i have make the solution to press boot when a upload the file and i use "esp 32 dev module "

shall you have the time to help me : i real want to make this diy , thanks a lot

ProjectsWithRed, 2022-09-28:
@Parang0n Hello, thank you!

I have made an update to the code, please upload again and let me know if you still have issues.

jagallja, 2022-10-22:
i have the same problem and can not figure the solution, and when i connect the z steppers the screen goes black

jagallja, 2022-10-22:
Hi @ProjectsWithRed
seem like the updated code still have issues in it, my 3 steppers still spinning on it own :(

ProjectsWithRed, 2022-10-27:
@jagallja Have you adjusted the bolt on the A4988 drivers to match your stepper motor drivers? Check this [link](https://lastminuteengineers.com/a4988-stepper-motor-driver-arduino-tutorial/) for the full explanation and how to adjust your drivers.

jagallja, 2022-11-02:
@ProjectsWithRed accidentaly solved this issue by lifting my PCB, it might short circuit or grounding. thank you for the awesome projects 👍

and i have one more problem, how do i reverse the direction of my extruder ? flipping the wire like 3D printer extruder doesnt work in it

Parang0n, 2022-11-03:
Hello sorry for the time , but i need to give you some information:

1st : the wire cutter WORK !!!! thank a lot it's a masterpiece.

2nd : it have a little bug but its not bad (70% of the time)  when you start the cutter, the 2 up/down motor make noise like they blocked , i think it come to the fact that the 2 motor have not the same position with wiring A and B  and the A4988 dont know what to do. don't worry i use the project like that

there is a picture of your invention !

thanks a lot !!!

[20221103_235406](https://user-images.githubusercontent.com/113788664/199850502-8984b071-835c-47af-8d34-2ef3b6bca27a.jpg)

ProjectsWithRed, 2022-11-08:
@Parang0n Perfect glad to hear its working now! To reverse the direction you can use negative steps. One way you can do it is change the `WIRE_MOVEMENT_MULTI` variable to be a negative value, for example, if it was 400, make it -400.

ProjectsWithRed, 2022-11-08:
@jagallja Perfect glad to hear its working now! To reverse the direction you can use negative steps. One way you can do it is change the WIRE_MOVEMENT_MULTI variable to be a negative value, for example, if it was 400, make it -400.

ProjectsWithRed, 2022-11-08:
@Parang0n That's awesome!! Thanks for sharing the picture, I love it!

The blade stepper motors might experience "blocking" as you said when they are not perfectly level when starting, so just make sure you calibrate them before turning on the machine. You can also look into changing the current for the stepper motors by adjusting the stepper motor drivers screw, see this [link](https://lastminuteengineers.com/a4988-stepper-motor-driver-arduino-tutorial/) which shows how to do that, ensure you are supplying the stepper motors sufficient current.

Closed 2023-04-16.

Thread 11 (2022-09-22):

No display

AV1987, 2022-09-22:
Hi @ProjectsWithRed.
Thanks for sharing this project, very interesting.
It seems I uploaded the code sucessful but I have no display. I only connect ESP32 Devkit with Oled 128x64.
The example code works ok with display. What do I miss?
Thank you

Tips: adding a 10uF Cap on RST pin to ground to avoid holding the Reset button during sketching.

ProjectsWithRed, 2022-09-28:
I have updated the code since there was an update to the `Encoder` library which made it not work. Upload again and let me know if you still have issues.

AV1987, 2022-09-28:
@ProjectsWithRed
Thank you. My display works now. But none of the motor runs and pulling 1.7A. It's hot the driver. Do you have this problem? I checked the wiring 2B,2A,1B,1A are correct and Calibration is false by default of your updated sketch.

AV1987, 2022-09-29:
> @AV1987 I have updated the code since there was an update to the `Encoder` library which made it not work. Upload again and let me know if you still have issues.

Thanks Red! My setup is running now. Will give you update.

AV1987, 2022-09-29:
Hi @ProjectsWithRed

I have everything is running now with your original updated code. However, the linear motion is running very slow and dragging not like your youtube video.
Please advise. Thanks

Closed 2022-09-30.

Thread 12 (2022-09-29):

Motor speed in slow motion

AV1987, 2022-09-29:
Hi @ProjectsWithRed
I got my setup is running, I leave everything same as your original sketch it seems matches with my calibration.
A new problem for me why these motors are moving very slow like "slow motion"
Please advise
Thanks

ProjectsWithRed, 2022-09-29:
Hello @AV1987, that's great to hear! Have you adjusted the A4988 stepper driver by turning the little bolt on it? That controlls how much current flows to the stepper motor, which may be causing the slow movement. Check this link which explains it well and how to adjust for your stepper motor.

AV1987, 2022-09-29:
Hi @ProjectsWithRed
I did try both increase current and voltage on 3x A4988 drivers. All of them slow like slow motion :)
Also, each of them pulling only 250mA
Whatelse could it be?

ProjectsWithRed, 2022-09-29:
What step configuration do you have on the A4988 drivers (the MS1, MS2, and MS3 pins)? You can also try to increase the speed of the motor by using these two variables, `LINMOT_STEPPERS_SPEED ` and `EXTRUDER_STEPPER_SPEED `.

ProjectsWithRed, 2022-09-30:
Can you link the exact motors used? Also, try increasing the `LINMOT_STEPPERS_SPEED ` and `EXTRUDER_STEPPER_SPEED ` variables.

AV1987, 2022-09-30:
@ProjectsWithRed
Good idea!
RTELLIGENT Nema 17 Stepper Motor 3PCS, 2 Phase Step Motor Bipolar 1.5A 59.5oz.in(42Ncm) 42x42x38mm 4-Wire 30cm Long Cable for 3D Printer (3, 42A02C-XH2.54) https://a.co/d/7eo0juY

AV1987, 2022-09-30:
@ProjectsWithRed
Forgot to quote your replied: yes i did change it to 200, that didn't help. Here's exactly problem when I turn it on (after uploaded sketch):
1. Humming noise from the motors when turn on, they're pulling 600mA.
2. No display until I press EN button on ESP32.
3. Press EN, the noise on motors is gone, no load. Display shows up. But slow motion still there when I run it.
Is it suppose to be normal?

`Can you link the exact motors used? Also, try increasing the LINMOT_STEPPERS_SPEED and EXTRUDER_STEPPER_SPEED variables.`

AV1987, 2022-09-30:
@ProjectsWithRed
!(https://user-images.githubusercontent.com/114119127/193358579-d41aae2e-6a1a-4ad1-a58e-ecf7f3f19b14.png)

ProjectsWithRed, 2022-10-27:
@AV1987 No its not normal. Are you sure you changed the bolt on the A4988 stepper drivers to the correct current for the motors? Check this [link](https://lastminuteengineers.com/a4988-stepper-motor-driver-arduino-tutorial/), which explains it in great detail.

Closed 2023-04-16.

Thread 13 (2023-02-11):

Step motor not turn  please help ...

JamerYou, 2023-02-11:
Hello sir i like to build this machine  but i got stuck here  the motor it not turn  even one step  , I check all connections everything exactly your picture diagram  then upload code but step motor not move  , display turn on good encoder work , but  all 3 step motor not even more , please help . Thank you .

ProjectsWithRed, 2023-03-22:
There could be a number of ways why this is the case and its hard to tell without knowing more information. However, things that come to mind are:
- To double check the wiring for the stepper motors.
- Ensure the stepper motor drivers you are using are rated for the stepper motors.
- Ensure you have adjusted the current limiter on each stepper motor driver to match the rated current of the stepper motors.
- Ensure that the enable pins are connected for each of the motor drivers, otherwise they will not work (see image below, black arrows).

If none of these points help, please share as much information as you can.

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

cwbullet, 2025-06-22:
I am having the same problem.  Is this project dead?

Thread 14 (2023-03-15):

software installation problem

Ackerley35, 2023-03-15:
I am getting an error like this. Can you help me?

Leaving...
Hard resetting via RTS pin...

Arduino IDE
Version: 2.0.4
CLI Version: 0.31.0

belenhed, 2023-03-21:
Hello maybe this can help?
https://randomnerdtutorials.com/solved-failed-to-connect-to-esp32-timed-out-waiting-for-packet-header/

ProjectsWithRed, 2023-03-22:
@Ackerley35 Are you holding down the boot button on the ESP32 when uploading the code? Also double check that you are using the correct board in the board manager in the Arduino IDE.

Ackerley35, 2023-03-22:
@ProjectsWithRed Despite that error, the program was loaded and this error did not matter. After checking their connections, the screen and stepper motors worked. But after a few tries, I think my esp32 module burned out :( When I try to upload it again by pressing the Boot button, I get an error "Failed uploading: uploading error: exit status 2". I think my card is probably broken and I'm planning to make software with arduino nano for now.
As if the ESP32 module is not very suitable. What do you think about this?

Also your idea is amazing and very simple. I congratulate you. Also sorry for my English, I have to answer with google translate.

belenhed, 2023-03-22:
Try to solder the cap 10 uF electrolytic capacitor between the EN pin and GND.

ProjectsWithRed, 2023-03-23:
> @ProjectsWithRed Despite that error, the program was loaded and this error did not matter. After checking their connections, the screen and stepper motors worked. But after a few tries, I think my esp32 module burned out :( When I try to upload it again by pressing the Boot button, I get an error "Failed uploading: uploading error: exit status 2". I think my card is probably broken and I'm planning to make software with arduino nano for now. As if the ESP32 module is not very suitable. What do you think about this?
>
> Also your idea is amazing and very simple. I congratulate you. Also sorry for my English, I have to answer with google translate.

That error doesn't necessarily mean the ESP32 is burned out. One way to check if it is, connect the ESP32 to power and see if the chip gets hot very quickly that you can't put your finger on it more than a couple of seconds, if that's the case then it might be burned out. If needed, share your wiring so we can see if there are any connections that might be causing the ESP32 to stop working.

No worries, I am glad to hear it!

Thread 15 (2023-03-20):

No display on turn on with DT pin on encoder

belenhed, 2023-03-20:
Hello

I made this and when I turn it on I got no display.
If I disconnect the dt pin of the encoder, and turn it on again I got display.
I manage to solve it putting and on off switch at the DT pin.
Turn it on whith the switch in off position and then when I got display turn the switch to on position for the encoder to work.
Do you have any ideas why I got this behavior?
Thanks

ProjectsWithRed, 2023-03-22:
I think this possibly has to do with the encoder library version used, or some small issue with wiring. Something to try is removing the line below in the `AutoWireCutterStripper.ino` file and see if the problem still persists.

https://github.com/ProjectsWithRed/auto-wire-stripper-cutter/blob/515eb32fa96801f713e04d3cdbdf00c595d80443/AutoWireCutterStripper/AutoWireCutterStripper.ino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

belenhed, 2023-04-02:
Hi I commented out the line but thew problem persist also I'm having issues sometimes it turns on and some times doesn't weird
I have to dc the esp from the headers and is back online

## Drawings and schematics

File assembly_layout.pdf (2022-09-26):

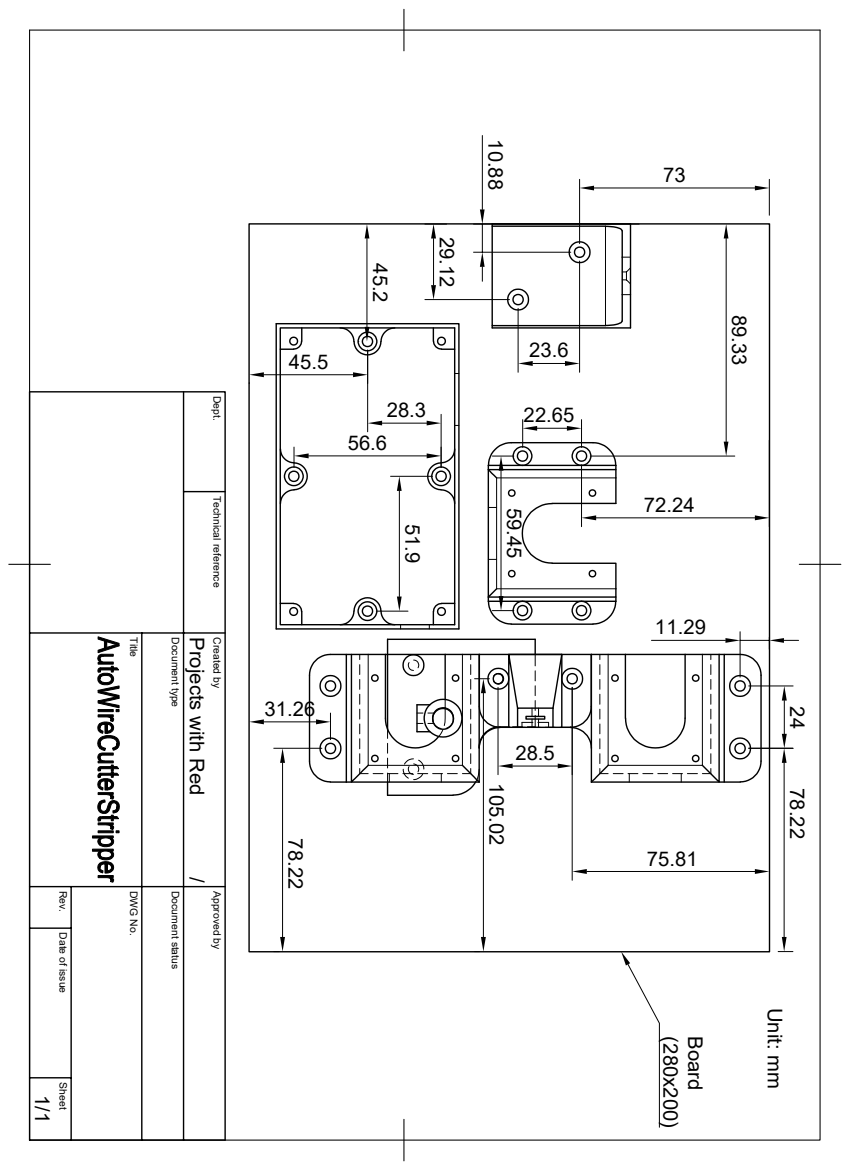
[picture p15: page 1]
Unit: mm ⁽²⁸⁰x200) Board

Dept. Technical reference Created by Approved by Title DWG No. Document type Document status Rev. Date of issue Sheet

/ 1/1 Projects with Red 24 78.2278.22

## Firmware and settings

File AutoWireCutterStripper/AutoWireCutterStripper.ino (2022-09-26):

#define ENCODER_DO_NOT_USE_INTERRUPTS
#include <Encoder.h>

#include <Stepper.h>
#include <SPI.h>
#include <Wire.h>
#include <Adafruit_GFX.h>
#include <Adafruit_SH110X.h>

#define motorInterfaceType 1
#define i2c_Address 0x3c


const int LINMOT_STEPPERS_STEP_PIN = 19;  // LINMOT: Linear motion
const int LINMOT_STEPPERS_DIR_PIN = 18;

const int EXTRUDER_STEPPER_STEP_PIN = 16;  // The stepper that moves the wire in the extruder.
const int EXTRUDER_STEPPER_DIR_PIN = 17;

const int ENCODER_DT_PIN = 0;
const int ENCODER_CLK_PIN = 23;
const int ENCODER_BTN_PIN = 4;

// For calibration only. The two buttons are used to move the top blade up and down manually.
// Once calibrated, you can remove the buttons from the circuit.
const int BTN1_PIN = 27;
const int BTN2_PIN = 26;

const int LINMOT_STEPPERS_STEPS = 1;  // Steppers step(s) movement at a time.
const int EXTRUDER_STEPPER_STEPS = 1;

const int LINMOT_STEPPERS_SPEED = 2000;
const int EXTRUDER_STEPPER_SPEED = 2000;


const int SCREEN_WIDTH = 128;  // OLED display width, in pixels
const int SCREEN_HEIGHT = 64;  // OLED display height, in pixels
const int TEXT_SIZE = 2;
const int TEXT_OFFSET = 3;

// Values for drawing the wire at the top of the OLED screen.
const int WIRE_STRAND_LENGTH = 30;
const int WIRE_STRAND_Y_POS = 7;
const int WIRE_INSULATION_WIDTH = SCREEN_WIDTH - (WIRE_STRAND_LENGTH * 2);
const int WIRE_INSULATION_HEIGHT = 14;

// These are just references to the corresponding component index in the comps array;
const int STRIPPING_LENGTH1_INDEX = 0;
const int WIRE_LENGTH_INDEX = 1;
const int STRIPPING_LENGTH2_INDEX = 2;
const int QUANTITY_INDEX = 3;
const int STRIPPING_DEPTH_INDEX = 4;
const int START_BTN_INDEX = 5;

const int CUTTING_STEPS = 17750;  // Steps to move blade to fully cut the wire.
const int STRIPPING_MULTIPLIER = 300;  // The chosen stripping depth value on the screen is multiplied by this value.
const int WIRE_MOVEMENT_MULTI = 408;  // How much to move wire per unit on OLED, turn on CALIBRATION_MODE to find this value.
const int DELAY_BETWEEN_CUTS = 100;  // Delay in ms between each cut in the quantity.

// To calibrate the wire movement distance. Use the first cell to enter the distance in mm to move the wire.
// Then adjust WIRE_MOVEMENT_MULTI to get the correct wire length.
const boolean CALIBRATION_MODE = false;


Stepper linMotSteppers(200, LINMOT_STEPPERS_DIR_PIN, LINMOT_STEPPERS_STEP_PIN);
Stepper extruderStepper(200, EXTRUDER_STEPPER_DIR_PIN, EXTRUDER_STEPPER_STEP_PIN);

Encoder encoder(ENCODER_DT_PIN, ENCODER_CLK_PIN);

Adafruit_SH1106G display = Adafruit_SH1106G(SCREEN_WIDTH, SCREEN_HEIGHT, &Wire, -1);


int linMotSteppersCurrStep = 0;  // Current position/step of the stepper motor.

// A component is a cell with a value on the OLED display.
struct Component {
    int x, y;  // Position
    int w, h;  // Size
    int value;  // Current value of the cell.
    boolean highlighted;  // Whether the cell is the currently highlighted cell.
    boolean selected;  // Whether the cell is currently the selected one, where its value will be controlled by the encoder.
    boolean btn;  // If it is a button or not.
};


Component comps[] = { {0, 20, 40, 20, 0, 0, 0, 0},
                     {44, 20, 40, 20, 0, 0, 0, 0},
                     {88, 20, 40, 20, 0, 0, 0, 0},
                     {0, 44, 40, 20, 0, 0, 0, 0},
                     {44, 44, 40, 20, 0, 0, 0, 0},
                     {88, 44, 40, 20, 0, 0, 0, 1} };

int numOfComps = sizeof(comps) / sizeof(comps[0]);


int encoderPos;  // Current position/value of the encoder.
int encoderLastPos;  // For OLED drawing.
int encoderLastPosMain;  // For main loop.

boolean encBtnState = false;
boolean encBtnPrevState = false;  // For OLED drawing.
boolean encBtnPrevStateMain = false;  // For main loop.



void setup() {
    linMotSteppers.setSpeed(LINMOT_STEPPERS_SPEED);
    extruderStepper.setSpeed(EXTRUDER_STEPPER_SPEED);

    pinMode(ENCODER_BTN_PIN, INPUT_PULLUP);

    pinMode(BTN1_PIN, INPUT_PULLUP);
    pinMode(BTN2_PIN, INPUT_PULLUP);

    display.begin(i2c_Address, true);
}


void loop() {
    int encPos = getEncoderPos();
    boolean encBtnState = digitalRead(ENCODER_BTN_PIN);

    // Only update OLED screen if encoder is moved or pressed.
    if ((encPos != encoderLastPosMain) || (encBtnState != encBtnPrevStateMain)) {
        handleOLEDDisplay();
    }

    if (comps[START_BTN_INDEX].selected) {
        runAutoCuttingStripping();
    }

    encoderLastPosMain = encPos;
    encBtnPrevStateMain = encBtnState;


    if (!digitalRead(BTN1_PIN)) {
        moveBlade(1);
    }
    if (!digitalRead(BTN2_PIN)) {
        moveBlade(-1);
    }
}


void handleOLEDDisplay() {
    display.clearDisplay();

    drawWire();

    boolean btnState = digitalRead(ENCODER_BTN_PIN);

    // Handling whether encoder is changing cell or value of the cell.
    if (!btnState && (btnState != encBtnPrevState)) {
        encBtnState = !encBtnState;

        if (encBtnState) {
            encoderLastPos = encoderPos;
        }
        else {
            encoder.write(encoderLastPos * 4);
        }
    }

    encBtnPrevState = btnState;

    if (!encBtnState) {
        encoderPos = getEncoderPos();
    }

    handleAllComponents();

    display.display();
}


void drawWire() {
    display.drawLine(0, WIRE_STRAND_Y_POS, WIRE_STRAND_LENGTH, WIRE_STRAND_Y_POS, SH110X_WHITE);
    display.fillRect(WIRE_STRAND_LENGTH, 0, WIRE_INSULATION_WIDTH, WIRE_INSULATION_HEIGHT, SH110X_WHITE);
    display.drawLine(WIRE_STRAND_LENGTH + WIRE_INSULATION_WIDTH, WIRE_STRAND_Y_POS, SCREEN_WIDTH, WIRE_STRAND_Y_POS, SH110X_WHITE);
}


void handleAllComponents() {
    for (int i = 0; i < numOfComps; i++) {
        Component& comp = comps[i];

        if (encoderPos == i) {
            comp.highlighted = true;

            if (encBtnState) {
                if (!comp.selected && !comp.btn) {
                    encoder.write(comp.value * 4);
                }

                comp.selected = true;

                int newEncPos = getEncoderPos();
                comp.value = newEncPos;

            }
            else {
                comp.selected = false;
            }

        }
        else {
            comp.highlighted = false;
            comp.selected = false;
        }

        drawComponent(comp);
    }
}


void drawComponent(Component comp) {
    if (comp.highlighted) {
        display.setTextColor(SH110X_BLACK, SH110X_WHITE);
        display.fillRect(comp.x, comp.y, comp.w, comp.h, SH110X_WHITE);

        if (comp.selected) {
            display.drawRect(comp.x - 1, comp.y - 1, comp.w + 2, comp.h + 2, SH110X_WHITE);
        }

    }
    else {
        display.setTextColor(SH110X_WHITE, SH110X_BLACK);
        display.drawRect(comp.x, comp.y, comp.w, comp.h, SH110X_WHITE);
    }

    if (comp.btn) {
        display.setTextSize(1);
        drawText("Start", comp.x + TEXT_OFFSET, comp.y + TEXT_OFFSET);
    }
    else {
        display.setTextSize(TEXT_SIZE);
        drawText(String(comp.value), comp.x + TEXT_OFFSET, comp.y + TEXT_OFFSET);
    }
}


void drawText(String text, int x, int y) {
    display.setCursor(x, y);
    display.println(text);
}


void runAutoCuttingStripping() {
    if (CALIBRATION_MODE) {
        moveWire(comps[STRIPPING_LENGTH1_INDEX].value);
        cut();
    }
    else {
        cut();
        delay(DELAY_BETWEEN_CUTS);

        for (int i = 0; i < comps[QUANTITY_INDEX].value; i++) {
            moveWire(comps[STRIPPING_LENGTH1_INDEX].value);
            strip();
            moveWire(comps[WIRE_LENGTH_INDEX].value);
            strip();
            moveWire(comps[STRIPPING_LENGTH2_INDEX].value);
            cut();
            delay(DELAY_BETWEEN_CUTS);
        }
    }

    comps[START_BTN_INDEX].selected = false;
    encBtnState = false;
}


void cut() {
    moveBlade(-CUTTING_STEPS);
    moveBlade(CUTTING_STEPS);
}


void strip() {
    moveBlade(-(comps[STRIPPING_DEPTH_INDEX].value * STRIPPING_MULTIPLIER));
    moveBlade(comps[STRIPPING_DEPTH_INDEX].value * STRIPPING_MULTIPLIER);
}


void moveBlade(int steps) {
    linMotSteppers.step(steps);
    linMotSteppersCurrStep += steps;
}


void moveWire(int steps) {
    extruderStepper.step(steps * WIRE_MOVEMENT_MULTI);
}


int getEncoderPos() {
    int encPos = encoder.read() / 4;
    return encPos;
}

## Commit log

2022-03-04 Update readme, add Arduino sketch.
2022-03-04 Add 3D models.
    [bottomBlade_housing.3mf, container.3mf, extruderStepper_housing.3mf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]
2022-05-23 Add assembly layout.
2022-07-25 Add oled display i2c address note
2022-08-01 Add note for ESP32 boot button on upload
2022-09-26 Add board size to assembly layout pdf
2022-09-26 Add gitignore and auto format arduino sketch
2022-09-26 Fix encoder interrupt issue
    [AutoWireCutterStripper.ino]
2022-11-24 Add stl 3d models.
    [bottomBlade_housing.stl, container.stl, extruderStepper_housing.stl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]
2023-04-16 Add assembly model design file.
